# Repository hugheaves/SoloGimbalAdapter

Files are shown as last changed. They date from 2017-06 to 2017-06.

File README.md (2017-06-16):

### Description ###

This is a customizable mounting adapter that allows you to mount a "generic" action camera roughly the same size as a GoPro in the 3DR Solo gimbal.

### Overview ###

There are four parts that are includde in this design: the actual adapter, a retaining clip to attach the adapter to the gimbal, a counterbalance weight for the back of the gimbal, and another weight for the side.

The adapter is pretty self-explanatory. You push the camera into the front of the adapter and it "snaps in". To remove the camera, just pull.

The retaining clip is designed to be installed in place of the green clip that comes pre-installed on the gimbal. Just unscrew the single screw that holds the green clip, install the printed retaining clip in the same place, and use the screw you just removed to secure the clip.

The weights are intended to balance the camera in the gimbal. Depending on the weight of your camera, they may not be needed. However, if you do print them, be sure to use 100% infill, otherwise they will not be heavy enough to work. The back weight screws into the the gimbal with three M2x6mm screws. There are screw holes in the back of the gimbal that line up with the holes in the weight.

### Customization ###

You'll definitely want to customize the adapter to be an exact fit for your camera, as not all of the GoPro type clones are the same size, and it won't work well if it's not a snug fit.

For example, the defaults are setup for a GitUp Git2P, which has the following dimensions:

* Length: 59.4mm
* Width: 41.1mm
* Height: 19.6mm

My no-name SJ4000 clone has the following dimensions:

* Length: 59.8mm
* Width: 40.8mm
* Height: 25.6mm  <--- big difference in height (thickness)

Also, if you're going to use the weights, you'll need to adjust the size for your camera. The defaults are, again, for a Git2P. If you're using a different camera, you'll just need to use some trial and error to get the weight size correct.

### Printing ###

All of the parts are designed to print without supports. The design will work in ABS or PLA. However, as PLA is a little "stiffer" than ABS, you may want to reduce the size of the bump" on the end of the retaining clips, otherwise it may be hard to insert and remove your camera.

It's also important to use a wall thickness that insures that the clips are solid and not hollow, as otherwise they will be too fragile. The clips are 3.2mm thick at the bottom so a 1.6mm wall thickness is good to use. (and works well with the commonly used 0.4mm nozzle size).

Also, given that orientation of the layers in the clips, your print is going to need good layer bonding / adhesion. Higher temperatures help with that - I printed my ABS at 240C, and PLA at 210C.

**Note:** Make sure to print the weights with 100% infill, otherwise they'll be too light weight to work properly.

### Links ###

The latest version of this model is available at
https://github.com/hugheaves/SoloGimbalAdapter

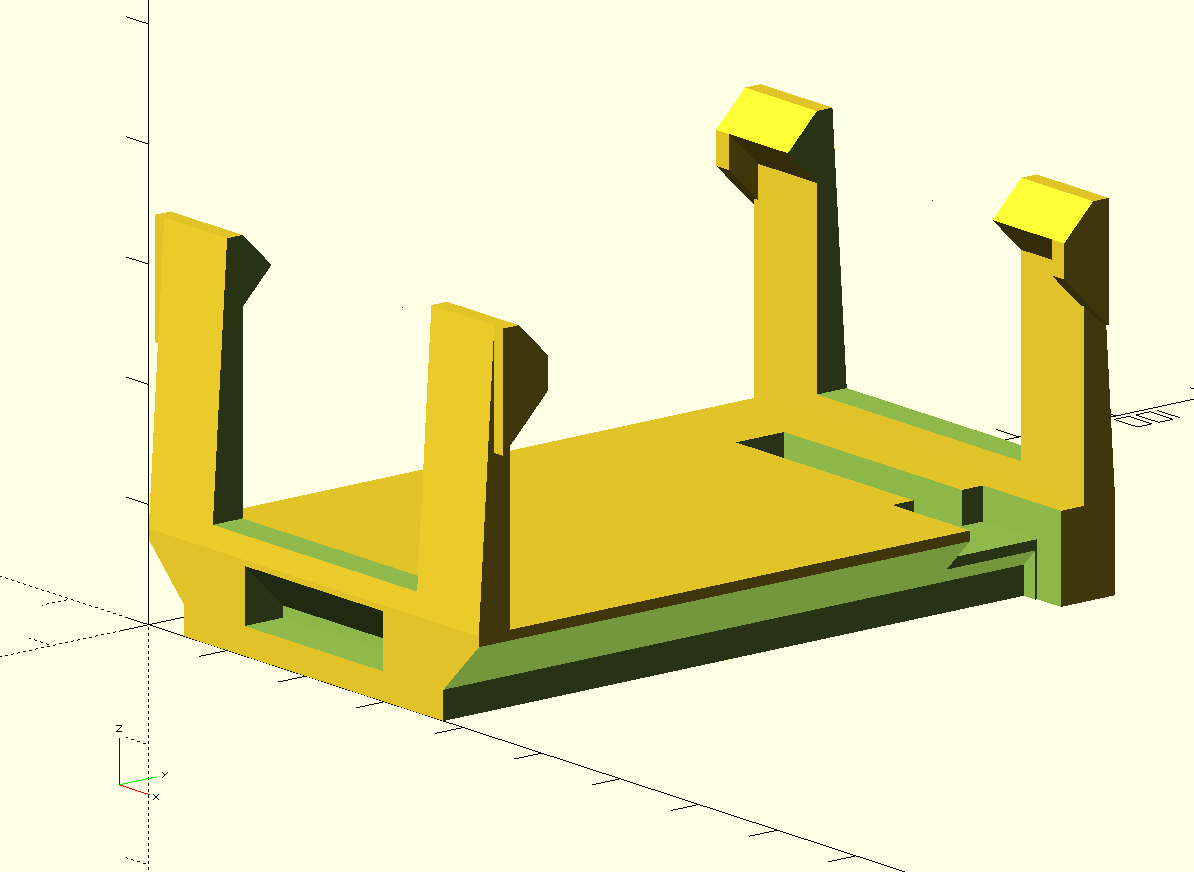
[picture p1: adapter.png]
Picture of Gimbal Adapter


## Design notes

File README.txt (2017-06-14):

This is an adapter that allows you to use any action camera roughly the same size as a GoPro with the 3DR Solo gimbal.

The design incorporates 45 degree angles in the overhangs so that it will print well without supports.

"main.scad" contains the main code for the adapter and the bracket. You can edit this file to customite the fit of the adapter to your camera.

Use "adapter.scad" and "bracket.scad" to actually print the adapter and the bracket. The bracket is designed to be installed in place of the green clip that comes with the gimbal. Just unscrew the single screw that holds the green clip, and install the bracket instead. You use the same screw that holds the green clip in place to secure the bracket.

"side_weights.scad" and "back_weight.scad" are 3D printed weights that you can use to balance the gimbal. You can edit the parameters in those files to change the size and therefore the weight of those weights. The side weights are designed to attach onto the exposed edge of the metal bracket on the opposide side from the camera. A single M2 screw and nut are used to hold them in place.

The latest version of this model is available at
https://github.com/hugheaves/SoloGimbalAdapter

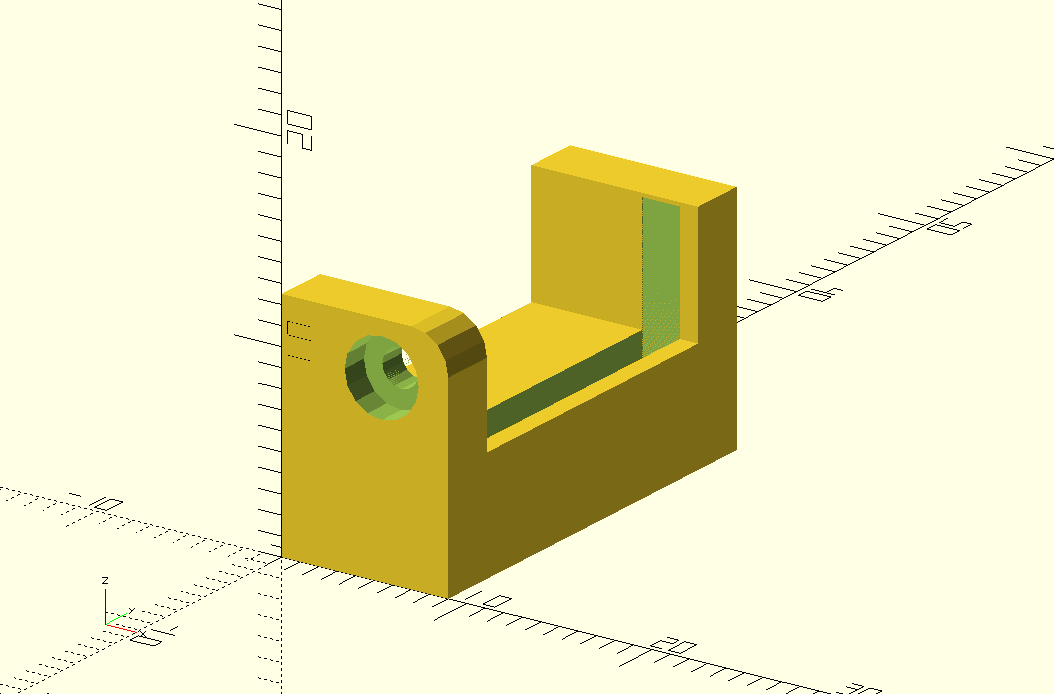
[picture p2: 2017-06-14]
bracket.png

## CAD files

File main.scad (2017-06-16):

/*
Generic Action Camera Adapter for 3DR Solo
Copyright (C) 2016 - 2017  Hugh Eaves

This program is free software: you can redistribute it and/or modify
it under the terms of the GNU General Public License as published by
the Free Software Foundation, either version 3 of the License, or
(at your option) any later version.

This program is distributed in the hope that it will be useful,
but WITHOUT ANY WARRANTY; without even the implied warranty of
MERCHANTABILITY or FITNESS FOR A PARTICULAR PURPOSE.  See the
GNU General Public License for more details.

You should have received a copy of the GNU General Public License
along with this program.  If not, see <http://www.gnu.org/licenses/>.
*/

/************************************************
 * PART SELECTION
 ************************************************/
 
// Select the part you would like to display
part = "adapter"; // [adapter:Adapter,retaining_clip:Retaining clip,back_weight:Back Weight,side_weight:Side Weight]

/********************
 * MAIN PARAMETERS *
 ********************/

// No-name SJ4000 clone
// camera_length = 59.8;
// camera_width = 40.8;
// camera_height = 25.6;

// The values below are for the GitUp Git2P

/* [Adapter Parameters] */
// Length of camera body (side to side)
camera_length = 59.4; // [57:62]
// Width of camera body (top to bottom)
camera_width = 41.1;  // [38:42]
// Height of camera body (front to back)
camera_height = 19.6;  // [15:40]

// Adapter arm bump size (How far out the "bumps" protrude on the ends of the arms)
adapter_arm_bump_size = 2.5; // [1:5]

/* [Back Weight Parameters] */
// The length of the counterbalance weight on the back of the camera. Larger values make it heavier.
back_weight_length = 29; // [10:40]

// The offset of the weight on the back of the gimbal. Values greater than zero move the weight to the outer side of the gimbal
back_weight_offset = 0; // [0:20]

/* [Side Weight Parameters] */
// The thickness of the side weight, thicker is heavier
side_weight_thickness = 4; // [4:8]

// The length of the side weight, longer is heavier
side_weight_length = 10; // [9:17]

/********************
 * OTHER PARAMETERS *
 ********************/
/* [Hidden] */

/* How much to shift the camera to the right to avoid the curved protrusion from the pitch motor housing */
camera_offset = 3.2;

/* Dimensions of the base of the camera adapter, so that it is a nice snug fit inside the 3DR gimbal mount */
base_height = 8;  // (thickness) thick enough to clear the GoPro plug in the back
base_width  = 42;
base_length = 60;

/* Dimensions of the small bracket that holds the camera adapter to the gimbal mount */
bracket_width = 9;
bracket_depth = 9.5;
bracket_thickness = 3;
bracket_radius = 2;

/* Typical values for M2 cap-head screws */
screw_thread_diameter = 2.5;
screw_head_diameter = 5;
screw_head_height = 3;

/* Dimensions of the "stud" that the 3DR balancing weights attach to */
stud_height = 2.5;
stud_diameter = 6.4;
stud_hole_diameter = 2;

bottom_lip_width = 4.5;
bottom_lip_height = 2.6;

// cutout for GoPro plug
plug_thickness = 5;
plug_width = 23;
plug_offset = 55.5 - (plug_thickness / 2);

// cutout for right side wall of "gimbal bracket"
side_wall_length = 31;
side_wall_height = 6.4;
side_wall_width = 3;
side_wall_offset = 59.4;

// height of hook on bottom left of "gimbal bracket"
hook_width = 17.6;
hook_height = 2.5; // distance from bottom
hook_length = 4;
hook_thickness = 1;

// width of protrusion on front of "pitch motor"
motor_protrusion_width = 20;

// thickness / length of camera retaining clips
clip_thickness = 1.6;
right_clip_opening_width =  26;
// left_clip_opening_width = motor_protrusion_width;
left_clip_opening_width = right_clip_opening_width;

x_midpoint = base_width / 2;
main_length = camera_length + camera_offset * 2;
camera_gap = (base_width - camera_width) / 2;

camera_height_adjustment = 0;

// more facets for smaller holes
$fn=16;

module lip_cutout() {
cube([bottom_lip_width, base_length, bottom_lip_height]);
  translate([0,0,bottom_lip_height])
  mirror([1,-1,0])
  wedge(base_length, bottom_lip_width, bottom_lip_width, false, false);
}


module side_wall_cutout() {
   translate ([0, side_wall_offset, 0]) {
      cutout_base_height = side_wall_height - (side_wall_width / 2);
      cube([side_wall_length, side_wall_width, cutout_base_height + 0.01]);
        translate([0,0,cutout_base_height])
        prism (side_wall_length, side_wall_width, side_wall_width / 2- 0.01);
    }
}

module hook_cutout() {
  translate ([x_midpoint - hook_width/2 ,0,hook_height]) {
    cube([hook_width,hook_length,hook_thickness]);
    translate([0,0,hook_thickness])
      wedge (hook_width, hook_length, hook_length, false); 
  }
}

module bracket_cutout() {
  bracket_clearance = 0.4;
  adj_bracket_width = bracket_width + bracket_clearance;
  adj_bracket_depth = bracket_depth + bracket_clearance;
  translate([base_width - bracket_depth, base_length + bracket_clearance / 2 - adj_bracket_width, 0]) {
    translate([-bracket_clearance,0,base_height - bracket_thickness])
      cube([adj_bracket_depth,adj_bracket_width,bracket_thickness + 5]);
    translate([bracket_depth - bracket_thickness,0,0])
      cube([bracket_depth,adj_bracket_width,base_height]);
  }

}

module clip_corner(length) {
    
  cube([clip_thickness, length + clip_thickness, length]);
    wedge(clip_thickness, length + clip_thickness, length + clip_thickness, false, true);
      
}


module clip(length) {
  cube([base_width,clip_thickness,camera_height]);
  translate([-clip_thickness + camera_gap,0,camera_height])
  cube([camera_width+clip_thickness*2,clip_thickness,length * 2 + camera_height_adjustment]);
  translate ([-clip_thickness + camera_gap, clip_thickness, camera_height + camera_height_adjustment])
    mirror([0,1,-1])
      prism(camera_width+clip_thickness*2,length*2,length);
 //   cube([camera_width+clip_thickness*2, length + clip_thickness, clip_thickness ]);
  wedge(base_width,camera_offset - clip_thickness,camera_height+ length * 2 + camera_height_adjustment, true, false);
  translate([0,0,camera_height + adapter_arm_bump_size + camera_height_adjustment - length]) {
  translate([-clip_thickness + camera_gap,0,0]) clip_corner(length);
  translate([base_width - camera_gap,0,0]) clip_corner(length);
  }
}

module left_clip() {
  translate ([0,camera_offset - clip_thickness,base_height]) {
    difference() {
      clip(adapter_arm_bump_size);
      translate ([x_midpoint - left_clip_opening_width / 2,-clip_thickness,2])
        cube([left_clip_opening_width,adapter_arm_bump_size + clip_thickness * 2,camera_height+adapter_arm_bump_size*2]);
    }
  }
}

module right_clip() {
  translate ([0,camera_length + camera_offset + clip_thickness,base_height]) {
    mirror ([0,1,0]) difference() {
      clip(adapter_arm_bump_size);
      translate ([x_midpoint - right_clip_opening_width / 2,-clip_thickness,2])
        cube([right_clip_opening_width,adapter_arm_bump_size + clip_thickness * 2,camera_height+adapter_arm_bump_size*2]);
    }
  }
}
     
module prism(x, y, z, upside_down){
  translate([0,y/2,0]) {
  wedge(x, y/2, z, true, upside_down);
  wedge(x, y/2, z, false, upside_down);
  }
}

module wedge(x, y, z, reverse, upside_down){
  ly = reverse ? -y : y;
  lz = upside_down ? -z : z;
  polyhedron(
    points=[[0,0,0], [x,0,0], [x,ly,0], [0,ly,0], [0,0,lz], [x,0,lz]],
    faces=[[0,1,2,3],[5,4,3,2],[0,4,5,1],[0,3,4],[5,2,1]]
  );
}

module weight_stud() {
  difference() {
    cylinder(d=stud_diameter - 0.4, h=stud_height, $fn=32);
    cylinder(d=stud_hole_diameter, h=stud_height, $fn=16);
  }
}


/********************************************
 * Top level function to render the adapter
 ********************************************/
module adapter() {

  difference () {
    cube([base_width, main_length, base_height]);
    
    lip_cutout();
    
    translate([base_width,0,0]) mirror([-1,0,0]) lip_cutout();
    
    side_wall_cutout();

    translate ([x_midpoint - plug_width/2, plug_offset ,0])
      cube([plug_width, plug_thickness, base_height]);

    hook_cutout();
    
    bracket_cutout();
  }
  
  left_clip();
  right_clip();
  
}

/********************************************
 * Top level function to render the retaining clip
 ********************************************/
module retaining_clip() {
  bracket_inside_height = 11.4 + base_height - bracket_thickness;
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

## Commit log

2017-06-14 Initial commit.
    [adapter.scad, back_weight.scad, bracket.scad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]
2017-06-14 Add preview to main.scad
    [adapter.scad, bracket.scad, main.scad]
2017-06-14 Add images Make adapter.scad actually render the adapter!
    [adapter.scad]
2017-06-16 Merged all models into one file. Added Thingiverse customizer support.
    [adapter.scad, back_weight.scad, bracket.scad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]
2017-06-16 Code cleanup and readme updates.
    [main.scad]
2017-06-16 Increased width of sidewall slot on adapter. Updated README. The width was increased to accomodate differences in printer calibration.
    [main.scad]
